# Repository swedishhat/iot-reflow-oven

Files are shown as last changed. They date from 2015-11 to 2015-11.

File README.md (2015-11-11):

# iot-reflow-oven
DIY solder reflow ovens. Internet of Toasters. So hot right now.

* doc -> AllAboutCircuits.com articles
    * 01_triac-dimmer -> [Control Your AC Mains with a Microcontroller](http://www.allaboutcircuits.com/projects/controlling-ac-mains-with-a-microcontroller-for-fun-and-profit/)
* sw  -> Software files
    * Atmega328P -> C files and headers for oven controller
* hw  -> Hardware files for TRIAC dimmer and contoller

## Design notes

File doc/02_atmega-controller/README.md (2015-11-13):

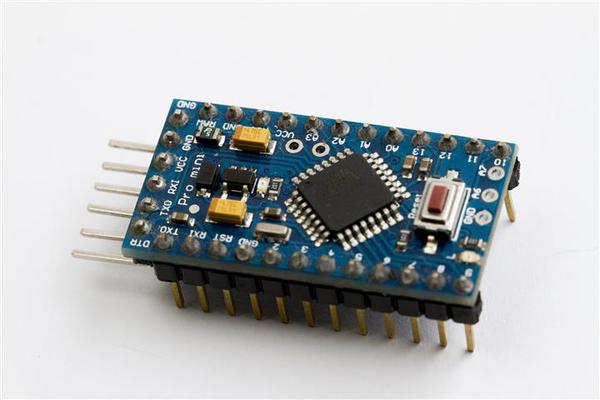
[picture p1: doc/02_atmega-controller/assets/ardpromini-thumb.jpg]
Look beyond the Arduino exterior, it's a raw ATmega underneath!


# Designing the Controller for a DIY Solder Reflow Oven
#### By [Patrick Lloyd](http://www.allaboutcircuits.com/author/patrick-lloyd)

## Summary
In the last installment, we built the hardware to control an AC waveform with a TRIAC as the first step in a DIY solder reflow oven. This tutorial continues the project by showing you how to set up the low-level hardware to measure temperature, read the zero-cross detector, drive the TRIAC, and print to the serial terminal using a USART.

#### Technical Concepts
* C programming
* Serial peripheral interface
* USART
* Internal and external interrupts
* Timers / counters

#### Introduction
**[See Part 1: Control Your AC Mains with a Microcontroller ](http://www.allaboutcircuits.com/projects/controlling-ac-mains-with-a-microcontroller-for-fun-and-profit/)**

Last time we built the TRIAC driver and zero-cross detection circuitry to interface with 120VAC mains voltages. It's a very capable bit of circuitry but without a proper controller, the end result wasn't all that interesting since it could only turn on or off the waveform, and not dim it. In this project, we are  writing C code on an Atmel ATmega328P microcontroller to accomplish several key tasks:
1. Read zero-cross signal with external interrupt and drive TRIAC with a special form of pulse-width modulation
2. Use the _Universal Synchronous and Asynchronous serial Receiver and Transmitter_ (USART) to display debug data
3. Interface with MAX31855 thermocouple amplifier over the _Serial Peripheral Interface_ (SPI)
4. Create a general purpose millisecond timer to help facilitate timeouts, timestamps, and non-blocking delays

Bare metal C means that we are writing very low-level code -- C is just a single step up from assembly language as far as abstraction goes. This means we'll be manipulating bits in specific registers, specifying interrupt vectors directly in our interrupt service routines (ISRs), and sometimes dealing with raw memory allocation with `malloc()`. There are some macros that make this process a little easier for us in `macros.h`(and make the code cleaner to read) but familiarity with some of the actual inner workings of the ATmega328P and the names it uses for different registers and components is very important. The [complete datasheet](http://www.atmel.com/images/Atmel-8271-8-bit-AVR-Microcontroller-ATmega48A-48PA-88A-88PA-168A-168PA-328-328P_datasheet_Complete.pdf)(PDF) for the chip has all that info in it and is worth keeping on hand. [Programming from the Gound Up](http://programminggroundup.blogspot.com/) may be a helpful resource as well for getting comfortable with low-level development.

_I'm using some code from [Andy Brown](http://andybrown.me.uk/) and his [ATmega8 oven controller](https://github.com/andysworkshop/awreflow2/tree/master/atmega8l). There is some drop-in code reuse, some tweaked bits, and some totally different implementations. In addition to having a different controller, he wrote his code in C++ and uses a different build system but I still want to give him full credit for the previous work he's done._

#### What You Need for this Project
This project is mostly software so the parts count is relatively small. You'll need:
* 3.3V ATmega328P microcontroller board with crystal oscillator (necessary for propery USART functionality)
  * [Arduino Pro Mini (3.3V)](http://www.digikey.com/product-detail/en/DEV-11114/1568-1054-ND/5140819) - I got a Chinese knock-off from Ebay instead of DigiKey. There are a bunch of small variations between boards so be aware when connecting your pins.
  * [Built your own](https://www.arduino.cc/en/Tutorial/ArduinoToBreadboard) - Plenty of tutorials out there on breadboarding your chip and doing a true barebones solution
* In-circuit Serial Programmer (ICSP)
  * [AVR Dragon](http://www.atmel.com/tools/AVRDRAGON.aspx) - I use this one. Lots of features and relatively cheap
  * [Arduino Uno](https://www.arduino.cc/en/Tutorial/ArduinoToBreadboard) - Other main Arduino boards can be used as a programmer as well.
* USB-Serial Adapter
  * [CH340/CH341](http://www.seeedstudio.com/wiki/USB_To_Uart_5V/3V3)
  * [FT232RL](https://www.sparkfun.com/products/10275) - **Needs to work at 3.3v!** I have this 5V model but I cut trace on the back and added a switch:

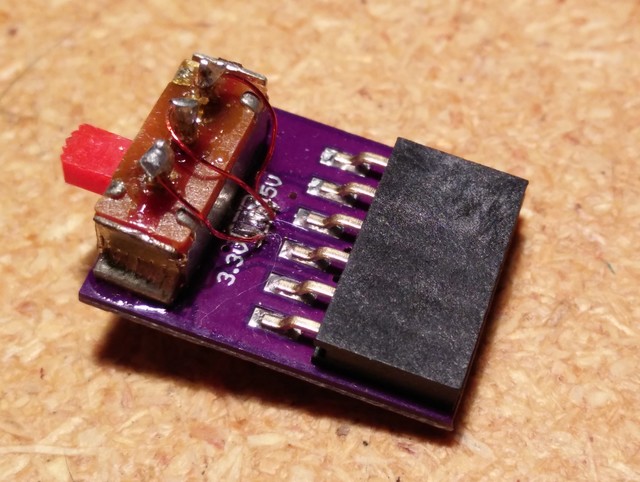
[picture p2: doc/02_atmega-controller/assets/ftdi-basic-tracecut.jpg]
Modified FTDI breakout


* MAX31855 breakout
  * [Home grown](http://www.allaboutcircuits.com/projects/build-a-thermocouple-amplifier-and-custom-kicad-libraries/)
  * [Adafruit](http://www.adafruit.com/product/269)
* Functioning TRIAC AC controller
* Computer running Linux with `avrdude`, `binutils-avr`, `gcc-avr`, `avr-libc`, and `gdb-avr` installed. It's possible to do this on Windows or Mac but that is outside the scope of this project.

#### TRIAC Controller
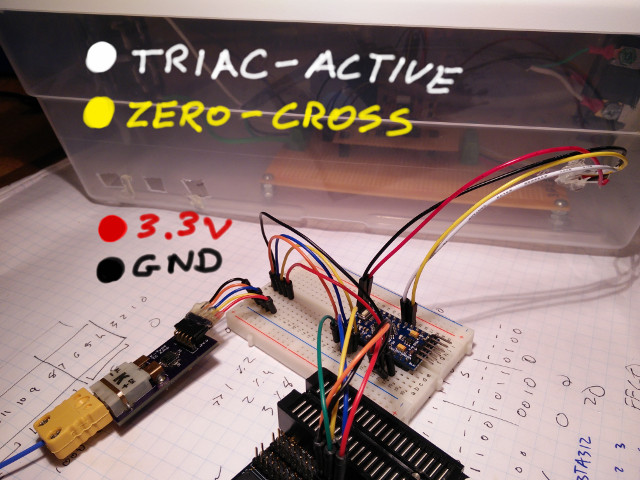
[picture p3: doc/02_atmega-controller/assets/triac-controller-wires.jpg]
Our controller connected to the box from last time


This is the bread and butter of the controller. The `oven_control.c` file consist of several parts: an `oven_setup()`, `oven_setDutyCycle(percent)`, and the three ISRs to deal with different timing-critical events.  

**Oven Controller Initization Function**
```c
void oven_setup(void)
{
    // Setup inputs and outputs
    CONFIG_AS_OUTPUT(TRIAC_EN);
    CONFIG_AS_INPUT(ZERO_CROSS);

    // Initial values for outputs
    SET_LOW(TRIAC_EN);

    // Configure external interrupt registers (Eventually move into macros.h)
    EICRA |= (1 << ISC01);      // Falling edge of INT0 generates an IRQ
    EIMSK |= (1 << INT0);       // Enable INT0 external interrupt mask

    // Enable Timer/Counter2 and trigger interrupts on both overflows & when
    // it equals OC2A    
    TIMSK2 |= (1 << OCIE2A) | (1 << TOIE2);
}
```

This function just sets up GPIO and interrupt conditions, as well as enabling Timer/Counter2.

**Output Intensity Function**
```c
void oven_setDutyCycle(uint8_t percent)
{

    uint16_t newCounter;

    // percentages between 1 and 99 inclusive use the lookup table to translate a linear
    // demand for power to a position on the phase angle axis
    if(percent > 0 && percent < 100)
        _percent = pgm_read_byte(&powerLUT[percent - 1]);

    // calculate the new counter value
    newCounter = ((TICKS_PER_HALF_CYCLE - MARGIN_TICKS - TRIAC_PULSE_TICKS) * (100 - percent)) / 100;

    // set the new state with interrupts off because 16-bit writes are not atomic
    cli();
    _counter_t2 = newCounter;
    _percent = percent;
    sei();
}
```

This function controls the output power of the oven and sets the timer wait value accordingly. The `powerLUT[]` array is used to map the linear percentage scale to a non-linear curve. With a linear scale, the actual power output change between 1% and 2% or 97% to 98% is significantly less than that at 50% to 51%. This is due to the sinusoidal nature of the quarter waveform we're dimming. This remapping lookup table helps to correct that -- see [Update 1: improving the phase angle timing](http://andybrown.me.uk/2015/07/12/awreflow2/) for more info. The PROGMEM attribute places the whole array into FLASH memory instead of RAM, saving space for the actual program. This will be useful for constant string storage as well later on in the series.

**Zero-Crossing Interrupt**
```c
ISR(INT0_vect)
{
    /* 0 is an off switch. round up or down a percentage that strays into the
     * end-zone where we have a margin wide enough to cater for the minimum
     * pulse width and the delay in the zero crossing firing */
    if(_percent == 0)
    {
        OVEN_OFF();
        return;
    }
    // either user asked for 100 or calc rounds up to 100
    else if(_percent == 100 || _counter_t2 == 0)
    {
        OVEN_ON();
    }
    // Comparison to a constant is pretty fast
    else if(_counter_t2 > TICKS_PER_HALF_CYCLE - TRIAC_PULSE_TICKS - MARGIN_TICKS)
    {
        // Also a constant comparison so also pretty fast
        if(_counter_t2 > (TICKS_PER_HALF_CYCLE - (TRIAC_PULSE_TICKS - MARGIN_TICKS / 2)))
        {
            // round half up to completely off
            OVEN_OFF();
            return;
        }
        else
            _counter_t2 = TICKS_PER_HALF_CYCLE - TRIAC_PULSE_TICKS - MARGIN_TICKS;
    }

    // Counter is acceptable, or has been rounded down to be acceptable
    OCR2A = _counter_t2;
    TCNT2 = 0;
    TCCR2B = (1 << CS20) | (1 << CS21) | (1 << CS22);    // start timer: 8MHz/1024 = 128uS/tick
}
```

This triggers on the falling edge of pin PD2. Depending on what the global `_percent` variable is set to, it will either turn the oven full on, full off, or set the Timer/Counter2 "Output Compare Register A" to a value corresponding to the "off time" after zero-cross interrupt fires. It then clears Timer/Counter2 and starts the timer.

**Timer/Counter2 Comparison Interrupt**
```c
ISR(TIMER2_COMPA_vect)
{
    // Turn on oven, hold it active for a min latching time before switching it off
    OVEN_ON();

    // The overflow interrupt will fire when the minimum pulse width is reached
    TCNT2 = 256 - TRIAC_PULSE_TICKS;
}
```

When the output comparison value is met, this interrupt is fired and it sets the TRIAC_ACTIVE pin high and loads up the TCNT2 register so that it overflows after TRIAC_PULSE_TICKS counts later.

**Timer/Counter2 Overflow Interrupt**
```c
ISR(TIMER2_OVF_vect)
{
    // Turn off oven
    OVEN_OFF();

    // turn off the timer. the zero-crossing handler will restart it
    TCCR2B = 0;
}
```

When the timer overflows, the TRIAC_ACTIVE pin goes low and the timer turns off, waiting for an INT0_vect to repeat the process.

#### USART
In normal C or C++ programming on a computer, functions like `assert()` and `sprintf()` can print formatted text to the terminal and help with debugging. In order to communicate with our device, we need to implement some way of printing to a terminal. The easiest way of doing that is through serial communication with the ATmega's USART and a USB-serial converter.

**USART Initialization Function**
```c
void usart_setup(uint32_t ubrr)
{
    // Set baud rate by loading high and low bytes of ubrr into UBRR0 register
    UBRR0H = (ubrr >> 8);
    UBRR0L = ubrr;

    // Turn on the transmission and reception circuitry
    UCSR0B = (1 << RXCIE0) | (1 << RXEN0 ) | (1 << TXEN0 );

    /* Set frame format: 8data, 2stop bit */
    UCSR0C = (1<<USBS0) | (3<<UCSZ00);

    // Use 8-N-1 -> Eight (8) data bits, No (N) partiy bits, one (1) stop bit
    // The initial vlaue of USCR0C is 0b00000110 which implements 8N1 by
    // Default. Setting these bits is for Paranoid Patricks and people that
    // Like to be reeeeeally sure that the hardware is doing what you say
    UCSR0C = (1 << UCSZ00) | (1 << UCSZ01);
}
```

In `usart.c`, there is the standard `usart_setup(uint32_t ubrr)` initialization function that enables the hardware and establishes the baud rate (bits/second) and transmission settings (8 data bits, no parity bits, 1 stop bit). This is hard-coded to 9600 baud for now in the `usart.h` file.

**Print Single Byte Function**
```c
void usart_txb(const char data)
{
    // Wait for empty transmit buffer
    while (!(UCSR0A & (1 << UDRE0)));

    // Put data into buffer, sends the data
    UDR0 = data;
}
```

This function accepts a single byte and when the transmit buffer is empty, loads the byte into the buffer. This is the basis for the other printing functions.

**Printing Helper Functions**
```c
/*** USART Print String Function ***/
void usart_print (const char *data)
{
    while (*data != '\0')
        usart_txb(*data++);
}
```
```c
/*** USART Print String Function with New Line and Carriage Return ***/
void usart_println (const char *data)
{
    usart_print(data);
    usart_print("\n\r");    // GNU screen demands \r as well as \n :(
}
```

Much like Arduino's Serial.print() and Serial.println() functions, these take a string as an argument and for each character, calls the `usart_txb()` function. `usart_println()` just has an extra step to print a new line and a carriage return.

**Interrupt on Receive**
```c
ISR(USART_RX_vect)
{
    unsigned char ReceivedByte;
    ReceivedByte = UDR0;
    UDR0 = ReceivedByte;
}
```

Right now there is no way to meaningfully interact with the software through the USART --  `ISR(USART_RX_vect)` was written as a placeholder for future development. When a character is received from the USB-serial converter, an interrupt is fired and it echos that same character to the output so it shows up on the screen.

#### General Purpose Timer
General delay and time comparison functions are very helpful in a lot of microcontroller applications. The `_delay()` function in `<avr/utils.h>` is helpful for small delays since it uses a while loop and `nop` instructions to do nothing for the specified amount of time. This prevents anything else from happening in the program, however. To deal with measuring longer blocks of time that allow for the program to continue, we use one of the free hardware timers and interrupts. On the ATmega328P, Timer/Counter0 is kind of gimpy and doesn't have as much functionality as Timer/Counter1 and Timer/Counter2 so it's a small triumph to be able to use it for something useful. We still have T/C1 but it would be nice to save it for something more complicated in the future.

**Timer Initization Function**
```c
void msTimer_setup(void)
{
    // Leave everything alone in TCCR0A and just set the prescaler to Clk/8
    // in TCCR0B
    TCCR0B |= (1 << CS01);

    // Enable interrupt when Timer/Counter0 reaches max value and overflows
    TIMSK0 |= (1 << TOIE0);
}
```

The first function is of course the initialization function. It sets the prescaler to 1 MHz and enables the overflow interrupt.

**Return Current System Time Function**
```c
uint32_t msTimer_millis(void)
{
    uint32_t ms;

    // NOTE: an 8-bit MCU cannot atomically read/write a 32-bit value so we
    // must disable interrupts while retrieving the value to avoid getting a
    // half-written value if an interrupt gets in while we're reading it
    cli();
    ms=_ms_counter;
    sei();

    return ms;
}
```

The msTimer functions chain together and all eventually call this function in some way. This simply returns the value of the global `_ms_counter` variable which is updated every millisecond.

**General Purpose Millisecond Delay Function**
```c
void msTimer_delay(uint32_t waitfor)
{
    uint32_t target;

    target = msTimer_millis() + waitfor;
    while(_ms_counter < target);
}
```

This is the `delay()` utility function. It accepts as an argument the amount of milliseconds you'd like it to wait for and blocks with a `while()` loop until finished. This should still only be used for short delays.

**Time Difference Measurement Function**
```c
uint32_t msTimer_deltaT(uint32_t start)
{
    // Return difference between a starting time and now, taking into account
    // wraparound
    uint32_t now = msTimer_millis();

    if(now > start)
        return now - start;
    else
        return now + (0xffffffff - start + 1);
}
```

Measures time delta between start time and current time. Can be used for delay loops that don't block. It also accounts for wraparound -- since time is saved in a 32-bit uint32_t variable, when it reaches 0xFFFFFFFF and increments, it rolls back around to zero. This factors that in to the calculation.

**Timeout Detection Function**
```c
bool msTimer_hasTimedOut(uint32_t start,uint32_t timeout)
{
    // Check if a timeout has been exceeded. This is designed to cope with wrap
    // around
    return msTimer_deltaT(start) > timeout;
}
```

True or false flag thrown when checking if a certain amount of time has passed. This is used in the temperature sensor so that you can call the `read()` function at whatever speed you want but it will only update according to its timeout interval.

**Timer/Counter0 Overflow Interrupt**
```c
ISR(TIMER0_OVF_vect)
{
    _ms_subCounter++;
    if((_ms_subCounter & 0x3) == 0) _ms_counter++;
    TCNT0 += 6;
}
```

The ISR running the show. Very accurately increments the global `_ms_counter` variable every millisecond.

#### Temperature Sensor
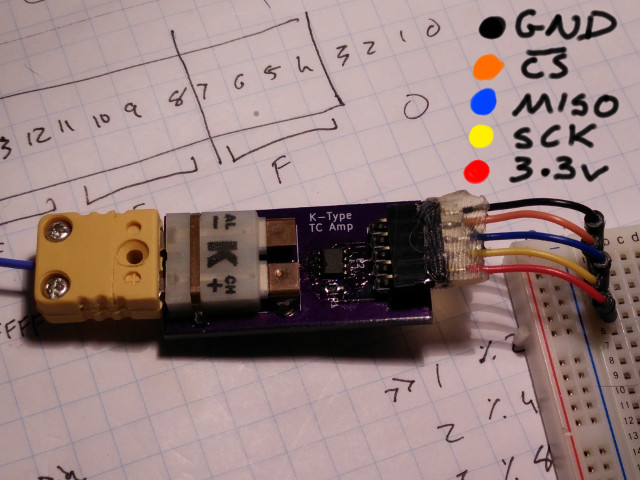
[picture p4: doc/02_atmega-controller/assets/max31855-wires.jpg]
My homemade MAX31855 board


The functions and data structures used to interface with the MAX31855 are a little different than the previous ones. I'm using a pseudo-object oriented paradigm where there is a structure named max31855 which is defined in `max31855.h`:

```c
typedef struct max31855
{
    int16_t     extTemp;        // 14-bit TC temp
    int16_t     intTemp;        // 12-bit internal temp
    uint8_t     status;         // Status flags
    uint32_t    lastTempTime;   // "Timestamp"
    uint32_t    pollInterval;   // Refresh rate of sensor
} max31855;
```

In `main.c`, a struct and a pointer to it are created and any time the temperature needs to be read or the values need to be printed to the USART, the struct pointer is passed as an argument to the different functions.

**Temperature Sensor "Object" Constructor**
```c
max31855 *max31855_setup(void)
{
    // Reserve some space and make sure that it's not null
    max31855 *tempSense = malloc(sizeof(max31855));
    assert(tempSense != NULL);

    // Initilaize struct
    tempSense->extTemp = 0;
    tempSense->intTemp = 0;
    tempSense->status = UNKNOWN;
    // Not sure why Andy Brown makes his last temp time start at 0xFFFFD8EF but
    // it works... Maybe it's to test timer0 wrap around / guarantee causality:
    // https://github.com/andysworkshop/awreflow2/blob/master/atmega8l/TemperatureSensor.h
    tempSense->lastTempTime = 0xFFFFFFFF - 10000;
    tempSense->pollInterval = DEFAULT_POLL_INTERVAL;

    // Set GPIO direction
    CONFIG_AS_OUTPUT(MAX31855_CS);
    CONFIG_AS_OUTPUT(MAX31855_MOSI);
    CONFIG_AS_OUTPUT(MAX31855_SCK);
    CONFIG_AS_INPUT(MAX31855_MISO);

    // Enable pullup on ~CS
    PULLUP_ON(MAX31855_CS);

    // Set outputs to default values
    SET_HIGH(MAX31855_CS);
    SET_LOW(MAX31855_MOSI);
    SET_LOW(MAX31855_SCK);

    // Enable SPI, Master, set clock rate fosc/4 (already default but we're
    // Paranoid Patricks over here and also like to make our code clear!)
    SPCR = (1 << SPE) | (1 << MSTR);
    SPCR &= ~((1 << SPR1) | (1 << SPR0)); // Not necessary............

    // Super speed 2x SPI clock powerup!
    SPSR |= (1 << SPI2X);

    return tempSense;
}
```

This is the "constructor" and initialization function for the max31855 struct. It reserves space in memory using `malloc()` and makes sure that it's not NULL. Since there is no `sprintf()` built into the AVR libraries by default, if the condition is true, it just aborts the program by forcing it into an endless loop. It then configures GPIO and turns on the hardware SPI peripheral.

**Read and Update Temperature Sensor Function**
```c
bool max31855_readTempDone(max31855 *tempSense)
{
    if(msTimer_hasTimedOut(tempSense->lastTempTime, tempSense->pollInterval))
    {
        uint8_t i;              // Loop index
        uint32_t rawBits = 0;   // Raw SPI bus bits

        // Bring ~CS low
        SET_LOW(MAX31855_CS);

        // clock 4 bytes from the SPI bus
        for(i = 0; i < 4; i++)
        {
            SPDR = 0;                           // start "transmitting" (actually just clocking)
            while(!(SPSR & (1 << SPIF)));       // wait until transfer ends

            rawBits <<= 8;                      // make space for the byte
            rawBits |= SPDR;                    // merge in the new byte
        }

        // restore CS high
        SET_HIGH(MAX31855_CS);

        // parse out the temp / error code from the raw bits. Are switch
        // statements bad? I dunno. Maybe. Who cares?
        uint8_t d = rawBits & 7;        // Are there any errors?
        if(!d)
        {
            tempSense->status = OK;
            // Only when tempterature is valid will it update temp. To get
            // Celcius integer, temp bits isolated with & bitmask, shifted
            // to right to align LSB (18 for extTemp, 4 for intTemp),
            // shifted to right again to get Celsius (extTemp = 0.25C per
            // bit >> 2; intTemp = 0.0625 C per bit >> 4)
            tempSense->extTemp = rawBits >> 20;
            tempSense->intTemp = (rawBits & 0x0000FFF0) >> 8;

            // Extend sign bit if negative value is read. In an oven. HA!
            if(tempSense->extTemp & 0x0800)
                tempSense->extTemp |= 0xF000;
            if(tempSense->intTemp & 0x0020)
                tempSense->intTemp |= 0xFFC0;
        }
        else
        {
            // Set temps to something obviously wrong
            tempSense->extTemp = -22222;
            tempSense->intTemp = -11111;

            // Which error code is it?
            switch(d)
            {
                case 1:
                    tempSense->status = OC_FAULT;
                    break;
                case 2:
                    tempSense->status = SCG_FAULT;
                    break;
                case 4:
                    tempSense->status = SCV_FAULT;
                    break;
                default:
                    tempSense->status = UNKNOWN;
                    break;
            }
        }

        // Update the timestamp and let the read loop unblock
        tempSense->lastTempTime = msTimer_millis();
        return true;
    }
    return false;
}
```

Designed to only refresh at the defined polling interval, this function leans heavily on the `msTimer_hasTimedOut()` function. If the timeout has been met, it clocks the SPI bus and reads in 32 bits of data. If the reading is valid and there aren't any error bits set, it parses out the temperature (both internal reference and external thermocouple) to the nearest integer. If there is an error, the temps are set to something obviously erroneous and the appropriate status flag is set.

**Status Message Helper Function**
```c
const char *max31855_statusString(uint8_t status)
{
    switch(status)
    {
        case UNKNOWN:
            return "UNKNOWN";
        case OK:
            return "OK!";
        case SCV_FAULT:
            return "SCV_FAULT";
        case SCG_FAULT:
            return "SCG_FAULT";
        case OC_FAULT:
            return "OC_FAULT";
    }
    return "Err";
}
```

Based on the status code, return a string to be printed with USART.

**Temperature Sensor Printing Function**
```c
void max31855_print(max31855 *tempSense)
{
    // max(int16_t) = "65535" + '\0'
    char buffer[6] = {0};

    usart_print("Status: ");
    usart_println(max31855_statusString(tempSense->status));

    usart_print("External Temp: ");
    usart_println(itoa(tempSense->extTemp, buffer, 10));

    usart_print("Internal Temp: ");
    usart_println(itoa(tempSense->intTemp, buffer, 10));
}
```

Convert the binary temperature value to decimal using the `itoa()` function and print using the USART.

#### Putting it All Together
The `main.c` file is just a small test file that initializes all the other parts through the `(device)_setup` command, flushes anything in the USART and then goes into an endless loop. In the loop, it fades the TRIAC drive intensity in and out and constantly tries to read the temperature. Since there's a poll interval specified in the `max31855_readTempDone()` function, it will only update and print status and temperature at that rate.

```c
/*** main.c ***/

#include "globals.h"

int main(void)
{
    // Globally disable interrupts
    cli();

    // Setup oven, timers, USART, SPI
    oven_setup();
    msTimer_setup();
    usart_setup(BAUD_PRESCALE);

    // Something kinda like OOP in C
    max31855 *m = max31855_setup();

    // Flush USART buffer
    usart_flush();

    // Clear interrupt flag by reading the interrupt register
    // Specify that it's 'unused' so compiler doesn't complain
    uint8_t dummy __attribute__((unused)) = SPSR;
    dummy = SPDR;

    // Turn on global interrupt flag
    sei();

    // "Hello World" startup message
    usart_println("Hot Toaster Action");

    // Main program loop
    for(;;)
    {                
        // "Fade" duty cycle in and out with single for loop
        int i = 0;
        int dir = 1;
        for (i = 0; i > -1; i = i + dir)
        {
            // Control power output
            oven_setDutyCycle(i);

            // Switch direction at peak and pause for 10ms
            if (i == 100) dir = -1;
            msTimer_delay(10);

            // If it's done reading, print the temp and status
            if(max31855_readTempDone(m)) max31855_print(m);
        }
    }

    return 1;
}
```

To finally compile and upload the code to the board, we use _GNU Make_. Make allows you to specify compiler and programmer options with a somewhat cryptic syntax. I borrowed the makefile template from [Pat Deegan at electrons.psychogenic.com](http://electrons.psychogenic.com/modules/arms/view.php?w=art&idx=8&page=2) and modified it to suit my needs. You may need to do the same if your setup differs from mine at all. The main things you should be concerned with are:

```
# Name of target controller
# ...
MCU=atmega328p
```
```
# ID to use with programmer
# ...
PROGRAMMER_MCU=atmega328p
```
```
# Name of our project
# ...
PROJECTNAME=iot-reflow-oven
```
```
# programmer id
# ...
AVRDUDE_PROGRAMMERID=dragon_isp
```
```
# port
# ...
AVRDUDE_PORT=usb
```

Once everything is to your liking, type `make` to compile and `sudo make writeflash` to upload to your board. If everything went according to plan, it should look something like this:

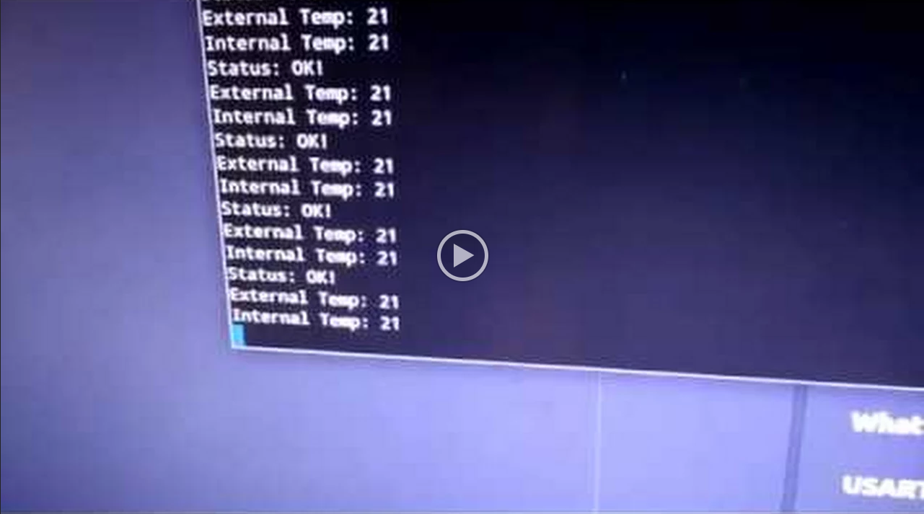
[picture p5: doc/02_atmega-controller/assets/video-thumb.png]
Click for video! (https://drive.google.com/file/d/0B3jahN8xZtrpVVhKWXJoeHd2cU0/view)


#### Conclusion

The next step is to get an actual toaster in the mix and start developing feedback controls for it. We're going to get into some control theory in the next article and write some test scripts to characterize the behavior of our system. That way we can create a robust, fast, and reliable controller regardless in the face of small perturbations and varying oven types. Keep hacking away at it, and like before, all source files can be found below or [on my Github page](https://github.com/swedishhat/iot-reflow-oven)-- feel free to collaborate. Cheers.

[atmega328p_2015-nov-13.zip](assets/atmega328p_2015-nov-13.zip)

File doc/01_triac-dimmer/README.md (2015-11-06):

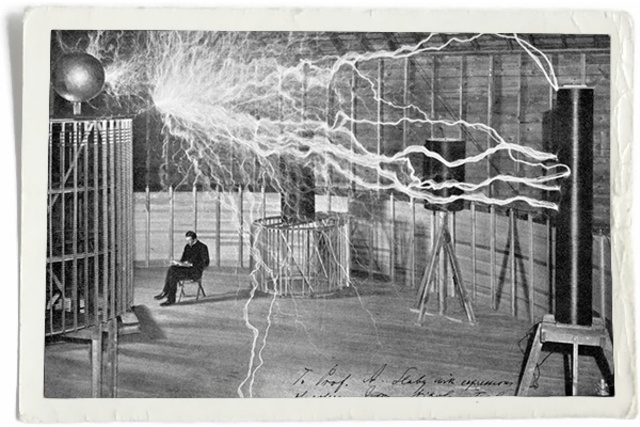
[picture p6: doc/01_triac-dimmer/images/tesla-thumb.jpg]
Good ol' Nick Tesla, Just Chillin'

# Controlling AC Mains with a Microcontroller for Fun and Profit
#### By [Patrick Lloyd](http://www.allaboutcircuits.com/author/patrick-lloyd)

## Summary
The first part of several on how to put together your own toaster oven controller with a handful of inexpensive, through-hole parts. The emphasis is on safety, low price, and minimal modification of the toaster oven.

## Technical Concepts
* High-voltage circuits
* TRIAC control
* Zero-crossing detectors
* Phase manipulation

## Introduction
The world is getting smaller and so are electronics designs. Through-hole components are less profitable for parts manufacturers and as a result, new products are often times only available in surface mount packages. Being able to solder surface mount parts by hand is a very valuable skill and can come in handy for parts like chip resistors and caps, small outline packages (SOIC/TSSOP), and quad flat packages (QFP). Still, what if the perfect ARM core for your quadcopter controller only comes as a quad-flat no-leads (QFN)? What if that FPGA you need to do vision processing with is only in a ball-grid array (BGA) style? You can take your chances with a hot air gun or you can use a solder reflow oven.

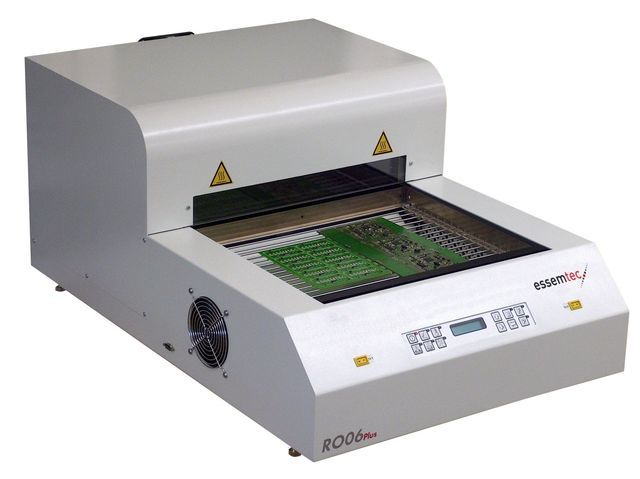
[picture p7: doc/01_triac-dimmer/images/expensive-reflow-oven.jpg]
Oooh shiny... But at what cost!?


_Oooh shiny... But at what cost!?_

Solder reflow ovens are nothing new, nor is making one for yourself out of a standard toaster like this one. The issue is that commercial options are generally very expensive (the one above may cost upwards of $2000 USD) and many home-built options often require the dismantling and modding the toaster which can be error prone and require special tools (my own [Black & Decker Toasr-R-Oven](http://www.amazon.com/gp/product/B00FN3MV88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) has security Torx screws in it...). Sparkfun [published a tutorial](https://www.sparkfun.com/commerce/tutorial_info.php?tutorials_id=60) back in 2006, Andy Brown [created a beautiful design](http://andybrown.me.uk/2015/07/12/awreflow2/) on his blog, and even AAC author [Robert Keim](www.allaboutcircuits.com/author/robert-keim) has some tutorials on the basic concepts of oven controlling such as [zero-cross detection](http://www.allaboutcircuits.com/projects/ambient-light-monitor-zero-cross-detection/) and [controlling a TRIAC](http://www.allaboutcircuits.com/projects/ambient-light-monitor-using-a-triac-to-adjust-lamp-brightness/). This set of tutorials aims to flesh out some of the concepts and provide a different hardware and (eventual) software approach to this application. It's another “recipe in the cookbook” if you will.

## What You Need
| Qty | Part | Price (USD) |
|:---:|:----:|:-----:|
| 1 | [Plastic enclosure](http://www.homedepot.com/p/Sterilite-6-Qt-Storage-Box-in-White-and-Clear-Plastic-16428960/203120094) | $1.24 |
| 1 | [IEC 10A plug with fuse holder and switch](http://www.ebay.com/itm/3-Pin-IEC320-C14-Inlet-Module-Plug-Fuse-Switch-Male-Power-Socket-10A-250V-TS-/231390116882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) | $3.99 |
| 2 | [10A glass fuses](https://www.digikey.com/product-detail/en/5ST%2010-R/507-1256-ND/1009028) | $0.44 |
| 1 | [15-Amp Tamper Resistant Single Outlet](http://www.homedepot.com/p/Leviton-15-Amp-Tamper-Resistant-Single-Outlet-White-R52-T5015-0WS/202066674) |$2.99 |
| 2 | [Six-position screw terminal block](https://www.digikey.com/product-detail/en/20020316-G061B01LF/609-3931-ND/2261342) | $3.50 |
| 1 | [47R 1/4 watt resistor](https://www.digikey.com/product-detail/en/CFR-25JB-52-47R/47QBK-ND/2219) | $0.10 |
| 1 | [180R 1/4 watt resistor](https://www.digikey.com/product-detail/en/CFR-50JB-52-180R/180H-ND/580) | $0.10 |
| 2 | [1K 1/4 watt resistor](https://www.digikey.com/product-detail/en/CFR-25JB-52-1K/1.0KQBK-ND/96) | $0.20 |
| 1 | [4.7K 1/4 watt resistor](https://www.digikey.com/product-detail/en/CF14JT4K70/CF14JT4K70CT-ND/1830366) | $0.10 |
| 1 | [22K 1/4 watt resistor](https://www.digikey.com/product-detail/en/CF14JT22K0/CF14JT22K0CT-ND/1830383) | $0.10 |
| 2 | [220K 1/4 watt resistor](https://www.digikey.com/product-detail/en/CF14JT220K/CF14JT220KCT-ND/1830407) | $0.20 |
| 1 | [100nF 275V X-class film capacitor](https://www.digikey.com/product-detail/en/ECQ-U2A104ML/P10730-ND/281393) | $0.65 |
| 1 | [1nF 1kV ceramic capacitor](https://www.digikey.com/product-detail/en/S102K29Y5PN63J5R/1251PH-ND/2356788) | $0.25 |
| 1 | [10uF 35V aluminum capacitor](https://www.digikey.com/product-detail/en/ESK106M035AC3AA/399-6598-ND/3083013) | $0.15 |
| 5 | [1N4148 (or equivalent) diode](https://www.digikey.com/product-detail/en/1N4007-TP/1N4007-TPMSCT-ND/773694) | $0.55 |
| 2 | General purpose NPN BJT ([2N3904](https://www.digikey.com/product-detail/en/2N3904BU/2N3904FS-ND/1413) or [2N5551](https://www.digikey.com/product-detail/en/2N5551BU/2N5551BU-ND/973957)) | $0.40 |
| 1 | [4N35 opto-isolator](https://www.digikey.com/product-detail/en/4N35/160-1304-5-ND/385766) | $0.48 |
| 1 | [MOC310 opto-isolator](https://www.digikey.com/product-detail/en/MOC3010M/MOC3010M-ND/284880) | $0.72 |
| 1 | [BTA312-600B TRIAC](https://www.digikey.com/product-detail/en/BTA312-600B%2FDG,127/568-9780-5-ND/2779860) | $0.99 |
| 1 | [TO-220 heatsink](https://www.digikey.com/product-detail/en/FA-T220-38E/FA-T220-38E-ND/2416492) | $1.60 |
| 1 | [T0-220 mounting hardware](https://www.digikey.com/product-detail/en/4724/36-4724-ND/109792) | $2.07 |
| 1 | [185V varistor](https://www.digikey.com/product-detail/en/MOV-20D201K/MOV-20D201K-ND/2799097) | $0.47 |
| 1 | Misc mounting hardware | ~ |
| 1 | Misc hookup wire | ~ |
|**TOTAL**| | ~$22.00 |

## A Few Notes on Safety
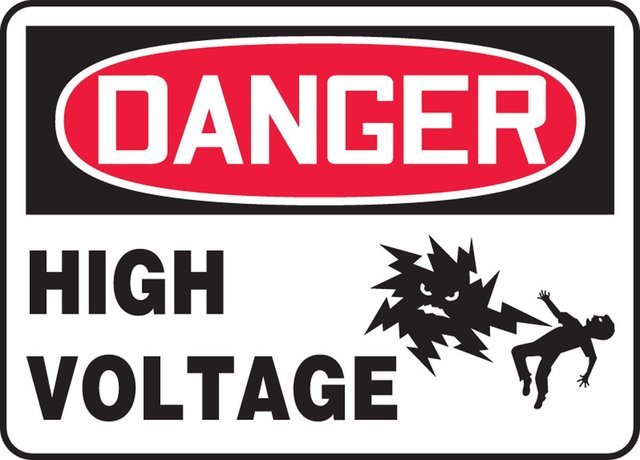
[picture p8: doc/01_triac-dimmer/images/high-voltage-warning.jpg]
Danger! Danger! High Voltage!


_That lightning monster is not messing around..._

A rock climbing instructor jokingly told me once that there are three rules to heed when it comes to safety. In order of priority, they are:

1. Look good.
2. Don't die.
3. If you have to die, look good doing it.

I promise you that you will be in violation of all three if you don't respect how dangerous mains voltages can be. There are a few things to keep in mind when dealing with high voltages:

* Don't connect high voltages to a breadboard. The risk of wires coming loose or accidentally touching / plugging into the wrong hole on a breadboard is not worth it. Soldering components to perfboard should be OK for prototyping though.

* Absolutely hands off whenever mains are connected. If you have to measure high voltages with your multimeter, don't hold the probes to the board by hand; attach alligator clips and operate the device remotely. Better yet, use an incandescent bulb as a test load and remotely turned on the device with a surge protector switch.

* Above all else, be smart about this. If you don't know what you are doing or don't feel comfortable doing it, ask for help and find someone who does. The AAC forums and local hackerspaces are great resources to leverage.

## System-Level Design
A full oven controller consists of several parts:

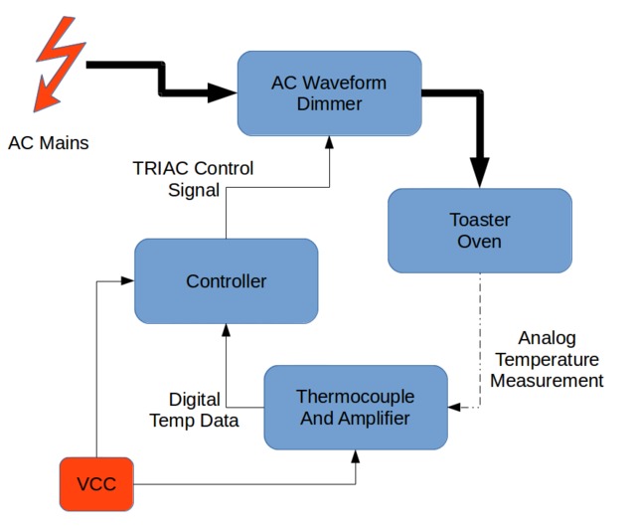
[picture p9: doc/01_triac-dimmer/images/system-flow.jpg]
System Flow Chart


_Toaster oven system flowchart_

We're only going to be making the AC waveform dimmer here. Note that this is an ad-hoc device in that it is designed to controlling __resistive loads only__, like most toaster ovens. Capacitive and inductive loads require some slight modifications (the addition of snubber components) which won't be covered here but information is available online and in the component datasheets. Compact fluorescent lamps (CFLs) have a fairly complicated electronic ballast circuit inside their housing that is not compatible with the AC dimmer at all.

A very common way of implementing an AC controller is with a solid-state relay. These allow the oven to be full ON or full OFF and the signal can be pulsed to get an approximate temperature (known colloquially as BANG-BANG controlling). A huge swath of the world's control systems run perfectly fine on BANG-BANG controllers but it is neither elegant nor super interesting to implement. Inside most solid state relays, however is a device called a TRIAC which can be ordered as a standalone device. Like Robert mentions [in his article](http://www.allaboutcircuits.com/projects/ambient-light-monitor-using-a-triac-to-adjust-lamp-brightness/), it's essentially a bidirectional extension of the thyristor, or can be though of as a solid-state switch that conducts current in both directions.

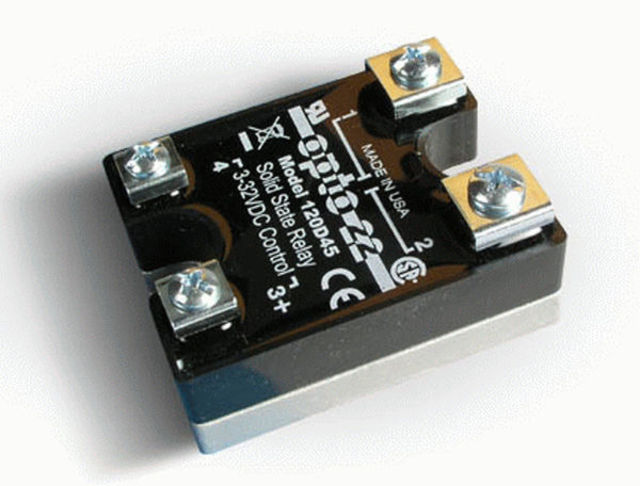
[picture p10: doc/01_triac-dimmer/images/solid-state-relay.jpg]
The Solid State Relay


_The solid state relay. Bang-bang, baby!_

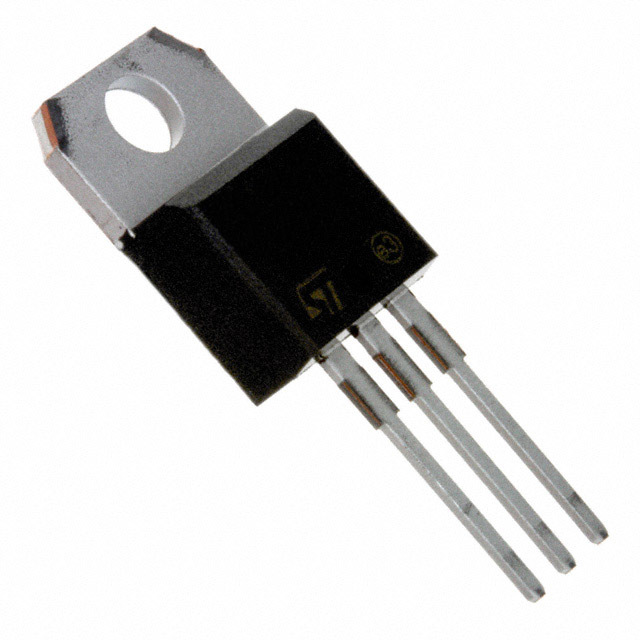
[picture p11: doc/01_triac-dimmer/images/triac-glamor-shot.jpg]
The TRIAC


_Not as flashy as the SSR but our TRIAC does some super cool stuff_

The whole idea of this oven controller is to use the TRIAC to implement something called [AC  phase control](https://en.wikipedia.org/wiki/Phase-fired_controllers). If you wait for the zero-crossing of the AC waveform and turn the TRIAC on at some known time later, you are left with an output waveform that retains the same frequency and magnitude of the original waveform for the time that the TRIAC is active. This limits the amount of power to the end device, effectively dimming it. Other methods of dimming exist like [wave packet control](https://de.wikipedia.org/wiki/Schwingungspaketsteuerung) (a sort of synchronous BANG-BANG paradigm; sorry no EN WikiPedia) but they are beyond the scope of this project.

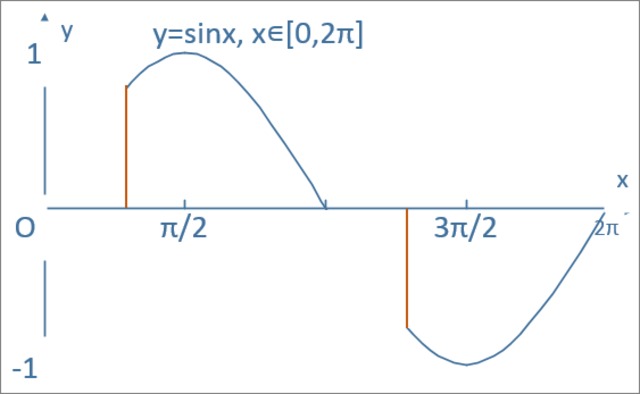
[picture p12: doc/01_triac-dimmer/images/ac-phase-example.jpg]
AC Phase Control in action


_Example of AC phase control from [Andy's Workshop](http://andybrown.me.uk/2015/07/12/awreflow2/)_

## Plugs, Terminals, and Enclosure
Safe and cheap is the name of the game here so the first order of business in making this was to select a reasonable enclosure. I got an inexpensive plastic bin with a lid and wrote a nice and scary warning label for myself and anyone around. Holes for the the plugs can be cut or drilled in the side but care needs to be taken to keep the material from cracking.

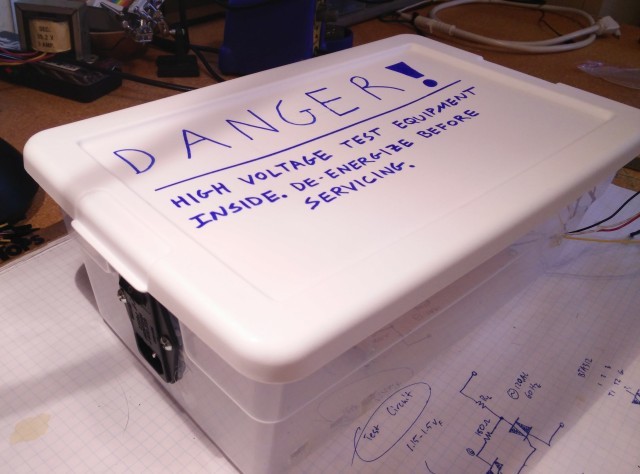
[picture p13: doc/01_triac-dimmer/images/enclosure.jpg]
Inexpensive plastic enclosure with lid and warning


I opted for a plug and socket interface to the dimmer. On the AC mains side, I used a 10A IEC plug with an integrated fuse holder (the fuses I had to source myself) and a power switch, much like this one:

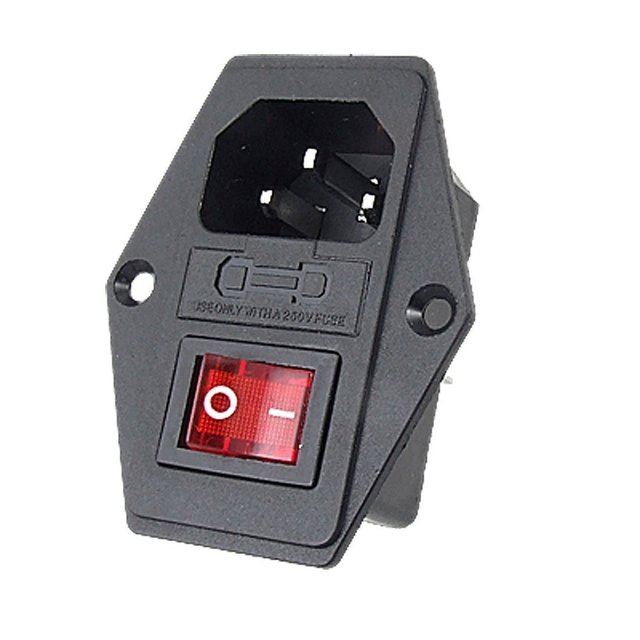
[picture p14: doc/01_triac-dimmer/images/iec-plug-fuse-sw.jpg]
10A IEC plug with integrated fuse holder and switch


_10A IEC plug with integrated fuse holder and switch_

It takes care of over-current protection and allows me to turn the whole thing off without having to unplug the cables. On the toaster side, I just browsed through my local hardware store and came upon this:

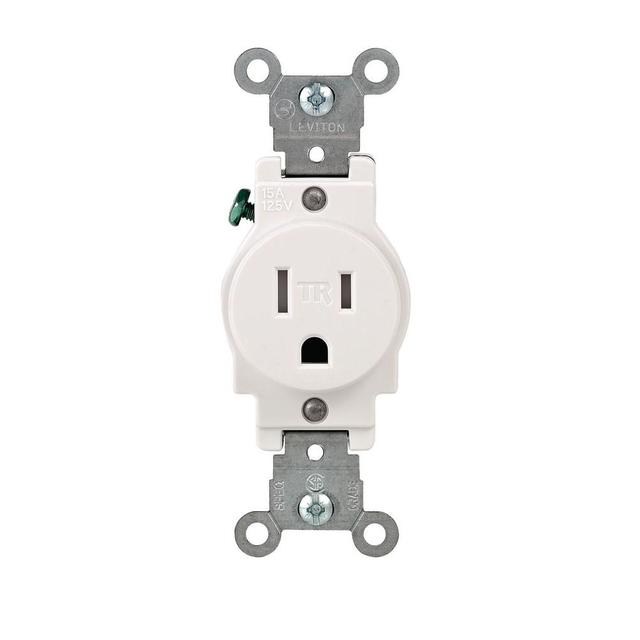
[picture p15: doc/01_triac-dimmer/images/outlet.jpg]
Single Tamper-Resistant Outlet


_Single tamper-resistant outlet_

It's a single tamper-resistant outlet that screws into the enclosure. I didn't want to solder the high voltage wires directly to my board so I got a six-position screw terminal block. The positions are for MAINS_L, MAINS_N, OVEN_L, OVEN_N, and two mains ground wires. I also used one of these terminal blocks for the four microcontroller wires leading outside of the box. A bit overkill but it's what I had on hand.

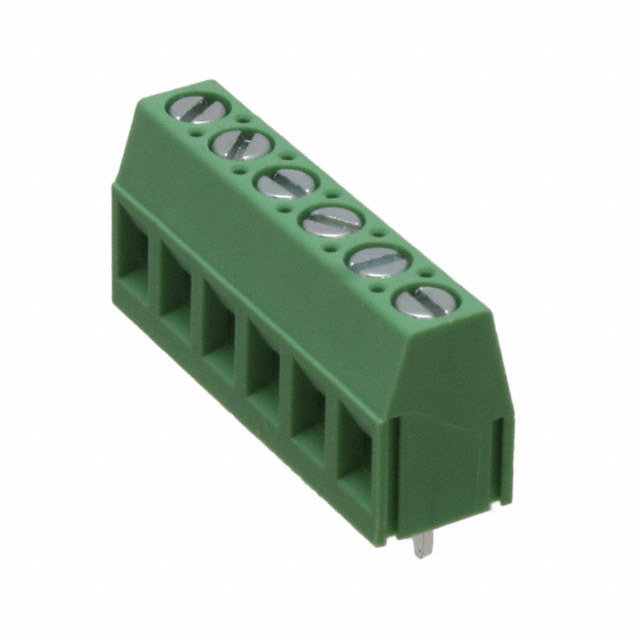
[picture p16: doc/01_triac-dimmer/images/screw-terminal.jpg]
Six-position Screw Terminal Block


## Isolated Zero-Crossing Detector
When controlling or measuring high voltage circuits with low voltage devices, it's always a good idea to employ some kind of galvanic isolation between the two sides; this can be accomplished either [inductively](https://en.wikipedia.org/wiki/Isolation_transformer), [optically](https://en.wikipedia.org/wiki/Opto-isolator), or  [capacitively](http://www.ti.com/lsds/ti/isolation/digital-isolators-overview.page). There are a few other isolation methods but these are the big ones.

Robert's [TRIAC controller](www.allaboutcircuits.com/projects/ambient-light-monitor-using-a-triac-to-adjust-lamp-brightness/) and [zero-crossing detector](www.allaboutcircuits.com/projects/ambient-light-monitor-zero-cross-detection/) use the transformer in a wall wart to step down the mains to a safer 12V before interacting with it. This application uses opto-isolators to separate the high and low voltages which has the advantage of being far lighter and more compact than a bulky transformer. They're slow to react to fast signal changes compared to some of the other methods but at sub-kilohertz speeds like our application, it doesn't really matter.

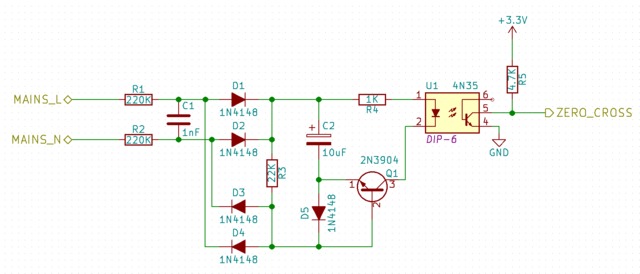
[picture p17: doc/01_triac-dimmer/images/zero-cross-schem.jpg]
Zero-crossing schematic


This circuit was [lovingly borrowed from here](http://www.dextrel.net/diyzerocrosser.htm). The author does an excellent job explaining the circuit in detail but a quick rundown goes like this: the mains waveform is first filtered and rectified. It's voltage is divided which then charges the 10uF cap. When the divided voltage drops below the voltage on the capacitor, the comparator transistor turns on, activating the opto-isolator. The output has an [open collector](https://en.wikipedia.org/wiki/Open_collector) which means you can operate it at any VCC your microcontroller supports. My perfboard circuit looks like this:

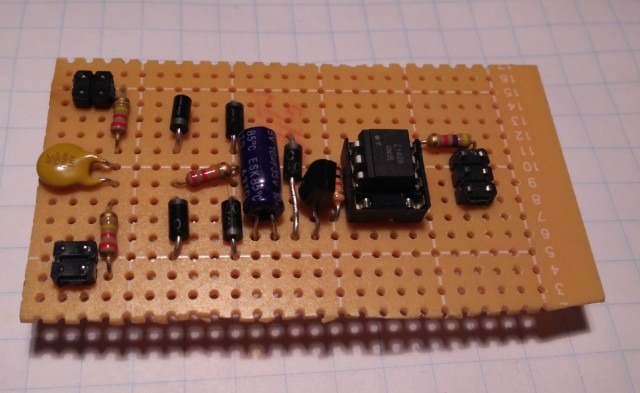
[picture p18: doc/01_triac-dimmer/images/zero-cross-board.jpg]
Perfboard zero-crossing detector


_A satisfyingly symmetrical circuit_

I tested this circuit in isolation from the rest of the board with a modified power cable and a surge protector. The zero-crossing detector waveform superimposed on an AC sinusoid should look something like this (I used a step-down transformer to get the shot. For the love of God don't hook your mains to your scope!):

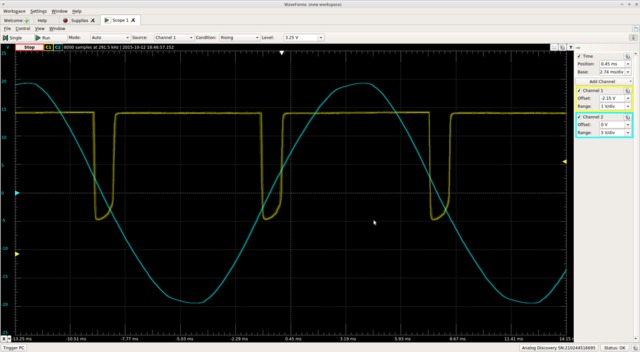
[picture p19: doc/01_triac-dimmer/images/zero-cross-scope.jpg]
Zero-crossing Detected!


## TRIAC Driver and Isolated Driver Circuit
Next up is the TRIAC and the isolated driver circuit. I mentioned earlier [Andy Brown's tutorial](http://andybrown.me.uk/wk/2015/07/12/awreflow2/). I adapted his TRIAC protection and driver circuit to work on 120VAC here in the States and followed his thermal considerations for heatsink selection. The TRIAC we're using is the [BTA312](http://www.nxp.com/products/thyristors/3_quadrant_triacs_high_commutation/BTA312-600B.html). We use another opto-isolator to drive the TRIAC called the [MOC310M](https://www.fairchildsemi.com/products/optoelectronics/triac-driver-optocouplers/random-phase-triac-driver/MOC3010M.html) which requires between 30 and 60mA to turn on. Most microcontrollers aren't comfortable sourcing this kind of current so we use a general purpose NPN transistor to provide it.

The schematic looks like this:

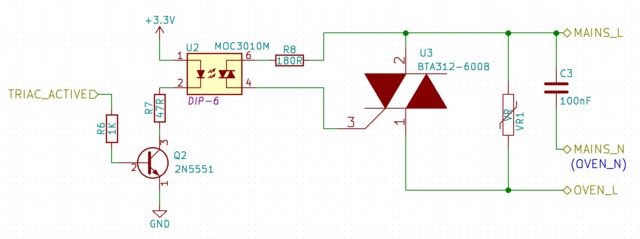
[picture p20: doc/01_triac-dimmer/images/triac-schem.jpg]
TRIAC Driver Schematic


VR1 is a varistor. It serves as over-voltage protection in case there's a spike in the AC line. C3 is a 275VAC film cap for emission suppression. That one could be considered optional. The MOC310 driver board circuit looks like this:

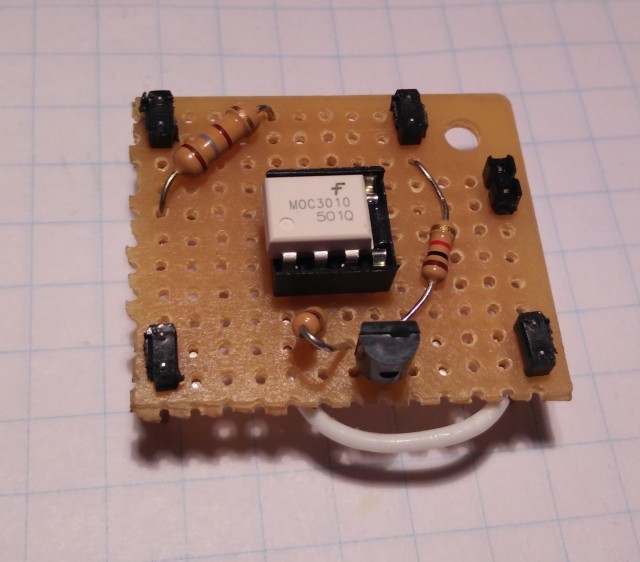
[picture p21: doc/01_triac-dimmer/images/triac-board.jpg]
TRIAC Driver Board


The heatsink, TRIAC, varistor, filter cap, and screw terminals all live on a main board separate from the driver. Once everything is attached to the board through headers, it should look something like this:

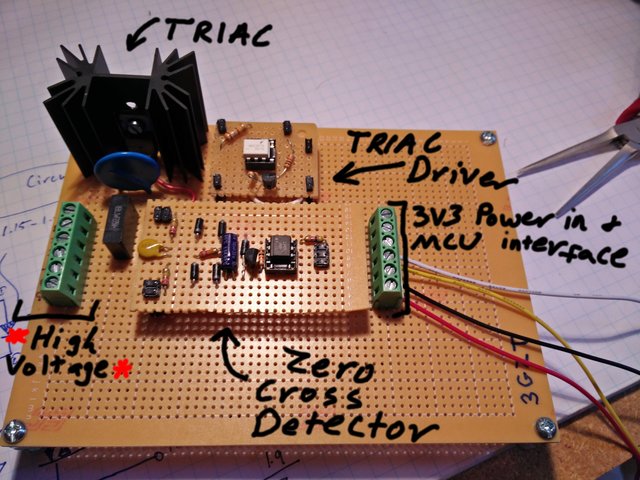
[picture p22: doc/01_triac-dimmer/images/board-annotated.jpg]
Main board annotated


I used the mounting holes at the corners of the main board to attach it to the enclosure. Once everything is put together you get this:

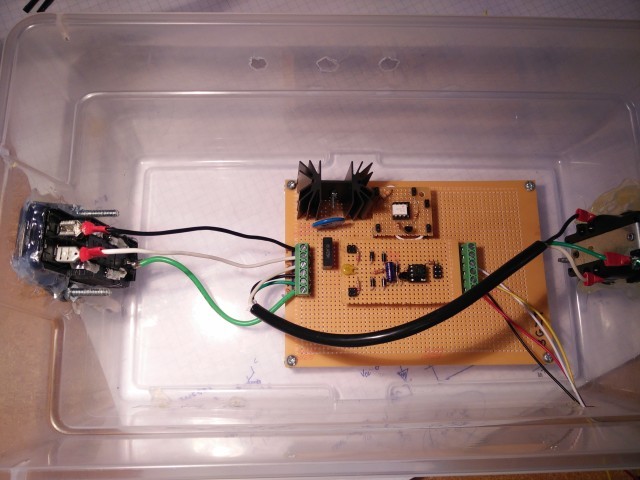
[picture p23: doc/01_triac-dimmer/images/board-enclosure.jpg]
Ready to roll!


Now you should be ready to roll! Connecting the wires appropriately ([this page was helpful](http://www.allaboutcircuits.com/textbook/reference/chpt-2/wiring-color-codes-infographic/)), connect up VCC and GND to a bread board power supply, and flip the power switch. If you apply 3.3V to the TRIAC_ACTIVE line, you should get 100% power on the other end.

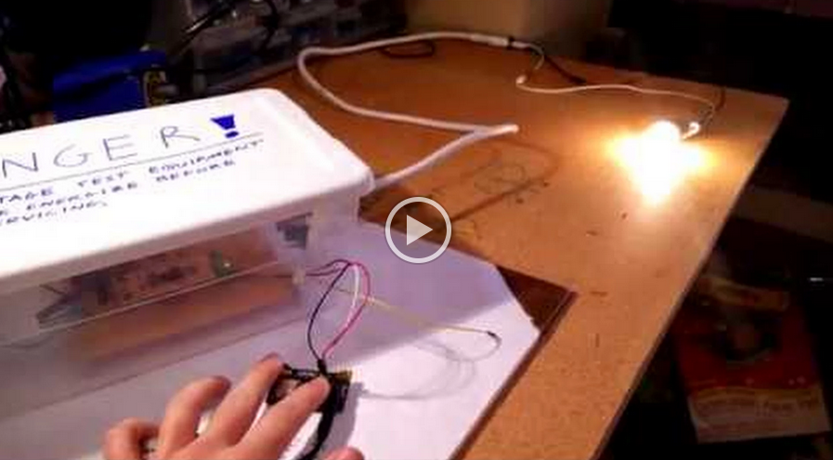
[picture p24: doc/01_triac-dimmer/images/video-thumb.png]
Click for video! (https://drive.google.com/file/d/0B3jahN8xZtrpay1hSzZTdWlmTjQ/preview)


## Next Steps
Okay, I admit it. Turning on a light bulb with a 3.3V switch isn't that impressive. In fact, it's pretty much just a BANG-BANG controller at that point. What we need next is a controller that can measure the zero-cross signal, dim the line accordingly, and read input from a temperature sensor. That will all be covered in the next installment. What's that you ask? Will I use an Arduino? __Absolutely not!__ It may look like that on the outside but we're going to be playing fast and loose with bare-metal C on the Atmega328P. Until next time, happy hacking.

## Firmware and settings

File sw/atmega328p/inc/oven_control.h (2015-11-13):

/*** oven_control.h ***/

#ifndef _OVEN_CONTROL_H_
#define _OVEN_CONTROL_H_

/*** I/O pins ***/
// Zero Cross Input
#define ZERO_CROSS              PD2
#define ZERO_CROSS_PORT         PORTD
#define ZERO_CROSS_DDR          DDRD
#define ZERO_CROSS_PIN          PIND

// TRIAC Enable Output
#define TRIAC_EN                PD3
#define TRIAC_EN_PORT           PORTD
#define TRIAC_EN_DDR            DDRD
#define TRIAC_EN_PIN            PIND

/*** TRIAC Timing Definitions ***/
/*
 * TRIAC timer runs at 128uS per 'tick' of TIMER2. The triac_pulse_ticks
 * variable defines how many ticks TRIAC gate will be activated for.
 * 4 ticks = 512uS
 */
#define TICKS_PER_HALF_CYCLE    65
#define TRIAC_PULSE_TICKS       4
#define MARGIN_TICKS            8

/*** Oven ON/OFF Macros ***/
#define OVEN_OFF()              SET_LOW(TRIAC_EN)
#define OVEN_ON()               SET_HIGH(TRIAC_EN)

/*** Oven Control Variables ***/
extern volatile uint8_t _percent;
extern volatile uint8_t _counter_t2;

void oven_setDutyCycle(uint8_t percent);

void oven_setup(void);
#endif

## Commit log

2015-11-05 more hw / sw / content. All articles are going to be markdown now... Stupid ass CMS ain't gon ruin my night no mo'git add .!
    [1-zero-cross.sch, kicad-triac-uc.kicad_pcb, kicad-triac-uc.sch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]
2015-11-06 Added .gitignore files to sw/ and hw/ and added parts table to dimmer article
    [1-zero-cross.sch, kicad-triac-uc.kicad_pcb, kicad-triac-uc.sch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]
2015-11-09 Modularized code, added power correction LUT, new Makefile with lots more features. Codebase ready for first software article.
    [main.c, oven_control.h]
2015-11-11 Added interrupt-driven USART echo mode
2015-11-12 usart, SPI temp sensor, timers, and triac controller all working in perfect harmony. Ready for article writeup.
2015-11-12 Added project folder for Hack-a-Day One Inch PCB contest. I call it MostToast
    [1-zero-cross.sch, controller.sch, most-toast-controller.kicad_pcb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]
2015-11-13 Added writeup on usart, timer/counters, and oven controller
2015-11-16 most-toast schematic finished.
    [controller.sch, most-toast-controller.sch, power.sch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]
